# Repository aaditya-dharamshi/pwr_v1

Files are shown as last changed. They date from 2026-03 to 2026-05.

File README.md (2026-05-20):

# pwr_v1
Main powerboard (first version) PCB files.

This was the first major board designed for SeeGoals, a project under FIA Robotics at Linkoping University, Sweden. I designed the complete PCB (assisted by other teammates who have developed the foundation), and the design files are shared here with permission from LiU SeeGoals.

This was the prototype for the main power distribution and interface board for the robot, powered by a 23.8V LiPo battery. This board is designed with KiCAD 8, and this repository contains the KiCAD project files and related documents.

# Documentations
📄 [Schematic PDF](Docs%20and%20Images/pwr_v1_schematic.pdf)
📄 [Layout PDF ](Docs%20and%20Images/pwr_v1_CopperLayers.pdf)

# 3D renders
Top view
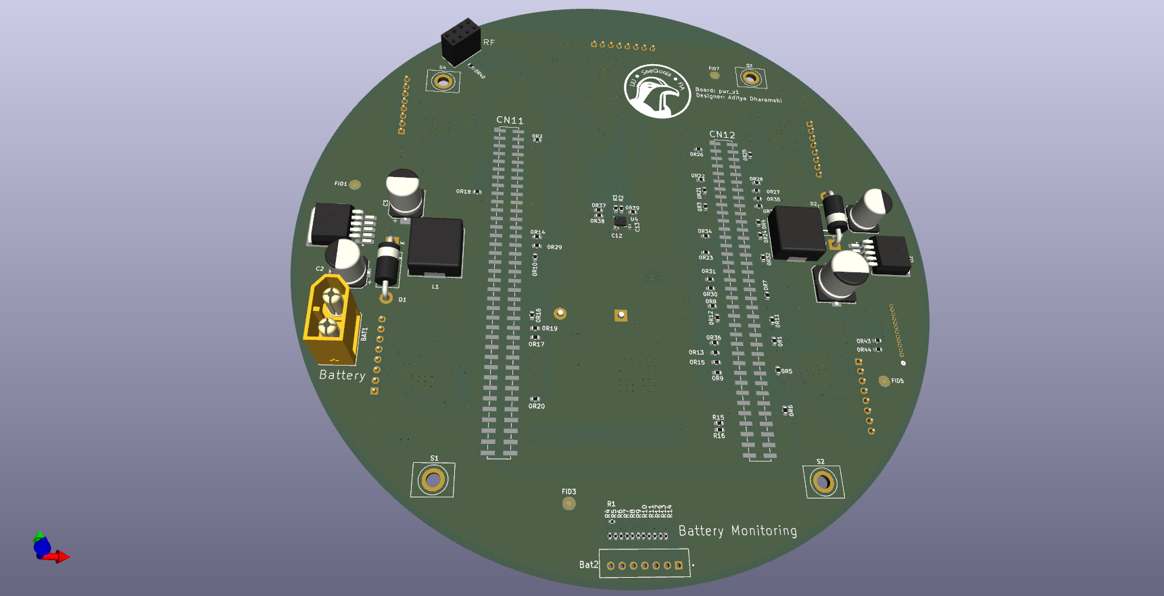
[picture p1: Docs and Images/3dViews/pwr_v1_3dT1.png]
Top Layer

Bottom view
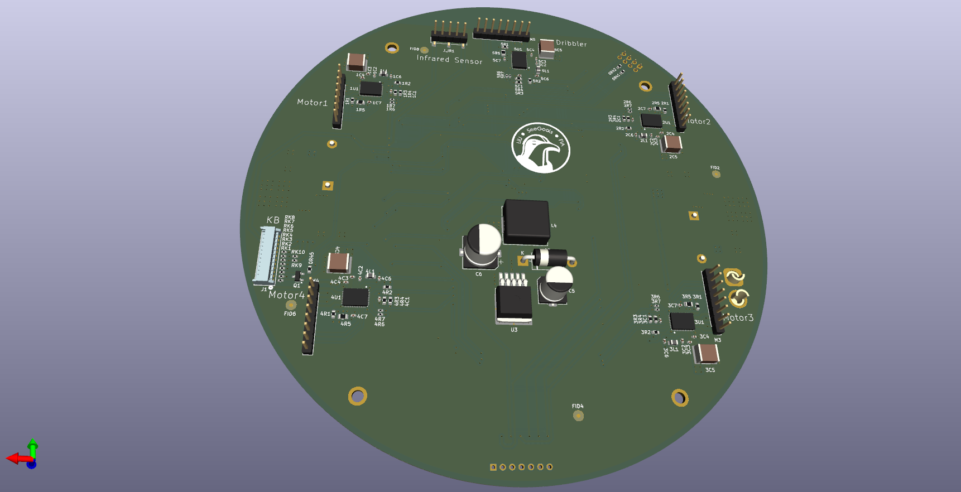
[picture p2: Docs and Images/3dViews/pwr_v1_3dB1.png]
Bottom Layer


Main features:
- 3.3V, 5V and 12V buck converters
- IMU on board
- Interfaces for STM32 Nucleo, nRF board and kicker board.

Stackup: 
- 4-layer FR4 PCB with 1.6mm thickness
- Copper thickness: 2 oz outer layer and 1 oz inner layers.

Design considerations:
- High-current power distribution from the LiPo battery.
- Dedicated power and signal layers.
- 4-layered stackup for improved grounding and power integrity.
- Decoupling capacitors placed carefully near the components.
- SMD-type connectors used for STM32 Nucleo interface, reducing thru hole pins and enabling better power and ground plane integrity.

Validation	
- This board was fabricated, assembled and integrated into the robot.
- During validation, issues related to nRF connector pin mapping, connector selection and mechanical design perspectivewere identified, which were addressed in the second revision.

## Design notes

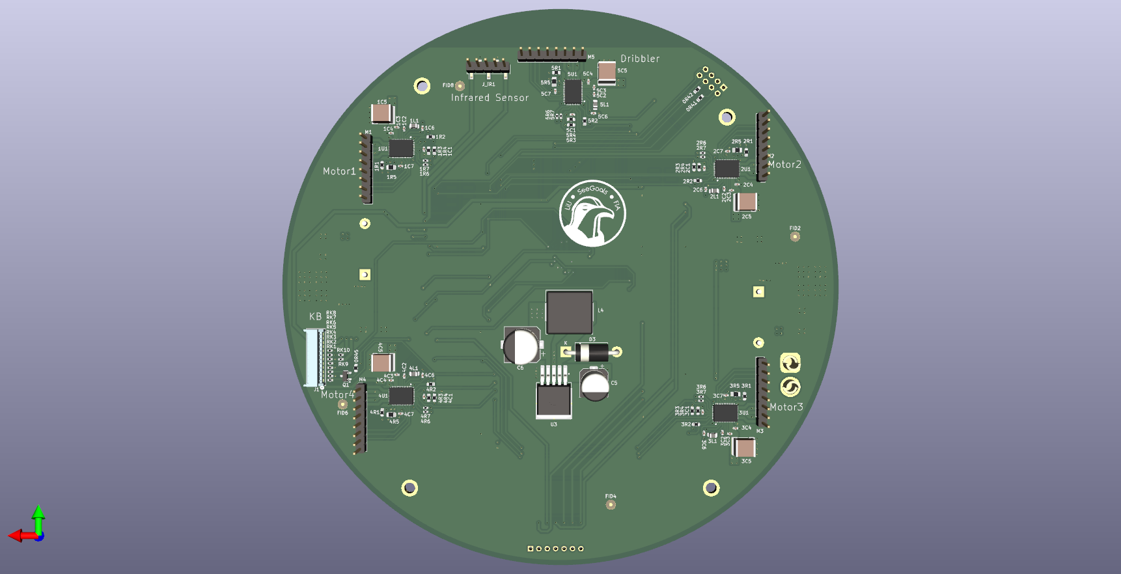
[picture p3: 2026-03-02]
Docs and Images/3dViews/pwr_v1_3dB.png

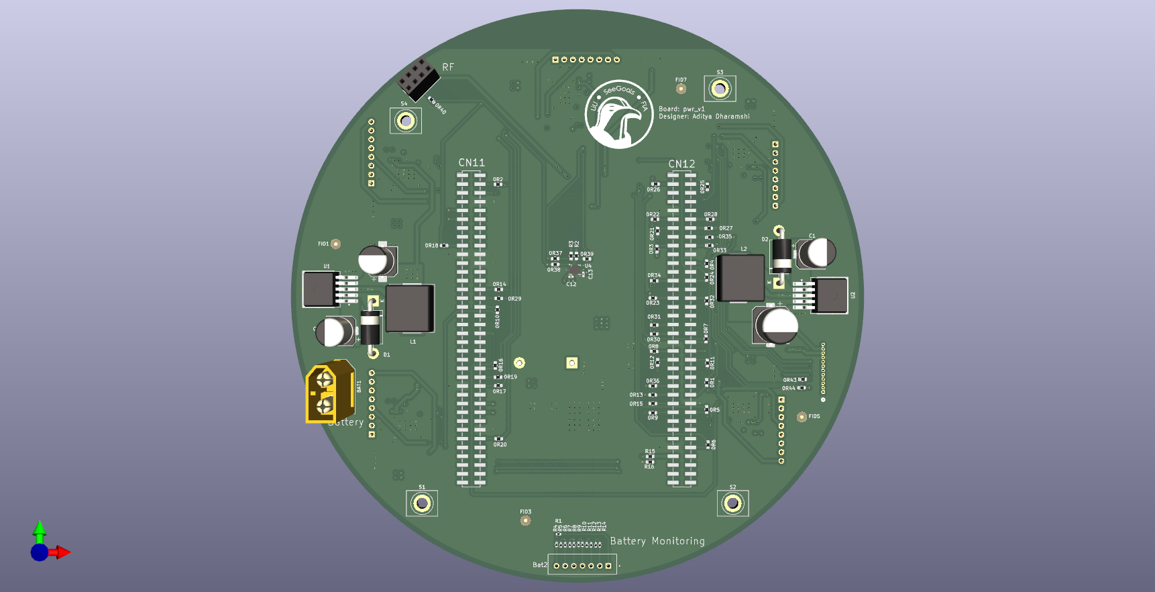
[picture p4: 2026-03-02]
Docs and Images/3dViews/pwr_v1_3dT.png

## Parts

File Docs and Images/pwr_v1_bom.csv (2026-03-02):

Value | Designator | Footprint | JLCPCB Part #?optional?
0 | 0R1,0R2,0R3,0R4,0R5,0R6,0R7,0R8,0R9,0R10,0R11,0R12,0R13,0R14,0R15,0R16,0R17,0R18,0R19,0R20,0R21,0R22,0R23,0R24,0R25,0R26,0R27,0R28,0R29,0R30,0R31,0R32,0R33,0R34,0R35,0R36,0R37,0R38,0R39,0R40,0R41,0R42,0R43,0R44,0R45 | Resistor_SMD:R_0603_1608Metric | C21189
100nF | 1C1 | Capacitor_SMD:C_0402_1005Metric | C1525
47nF | 1C2 | Capacitor_SMD:C_0402_1005Metric | C307339
1uF | 1C3 | Capacitor_SMD:C_0402_1005Metric | C14445
0.1uF | 1C4 | Capacitor_SMD:C_0402_1005Metric | C307331
22uF | 1C5 | Capacitor_SMD:C_2220_5750Metric | C784103
22uF | 1C6 | Capacitor_SMD:C_0402_1005Metric | C105226
1uF | 1C7 | Capacitor_SMD:C_0402_1005Metric | C76999
47uH | 1L1 | Inductor_SMD:L_0805_2012Metric | C105499
5k1 | 1R1,1R2 | Resistor_SMD:R_0603_1608Metric | C403509
27k | 1R3 | Resistor_SMD:R_0603_1608Metric | C22967
20k | 1R4 | Resistor_SMD:R_0603_1608Metric | C4184
1M | 1R5 | Resistor_SMD:R_0805_2012Metric | C107700
47k | 1R6 | Resistor_SMD:R_0402_1005Metric | C25792
22k | 1R7 | Resistor_SMD:R_0402_1005Metric | C25547
MCT8316Z0TRGFR | 1U1 | motorDriver:RGF0040E-IPC_B | C3681342
100nF | 2C1 | Capacitor_SMD:C_0402_1005Metric | C1525
47nF | 2C2 | Capacitor_SMD:C_0402_1005Metric | C307339
1uF | 2C3 | Capacitor_SMD:C_0402_1005Metric | C14445
0.1uF | 2C4 | Capacitor_SMD:C_0402_1005Metric | C307331
22uF | 2C5 | Capacitor_SMD:C_2220_5750Metric | C784103
22uF | 2C6 | Capacitor_SMD:C_0402_1005Metric | C105226
1uF | 2C7 | Capacitor_SMD:C_0402_1005Metric | C76999
47uH | 2L1 | Inductor_SMD:L_0805_2012Metric | C105499
5k1 | 2R1,2R2 | Resistor_SMD:R_0603_1608Metric | C403509
27k | 2R3 | Resistor_SMD:R_0603_1608Metric | C22967
20k | 2R4 | Resistor_SMD:R_0603_1608Metric | C4184
1M | 2R5 | Resistor_SMD:R_0805_2012Metric | C107700
47k | 2R6 | Resistor_SMD:R_0402_1005Metric | C25792
22k | 2R7 | Resistor_SMD:R_0402_1005Metric | C25547
MCT8316Z0TRGFR | 2U1 | motorDriver:RGF0040E-IPC_B | C3681342
100nF | 3C1 | Capacitor_SMD:C_0402_1005Metric | C1525
47nF | 3C2 | Capacitor_SMD:C_0402_1005Metric | C307339
1uF | 3C3 | Capacitor_SMD:C_0402_1005Metric | C14445
0.1uF | 3C4 | Capacitor_SMD:C_0402_1005Metric | C307331
22uF | 3C5 | Capacitor_SMD:C_2220_5750Metric | C784103
22uF | 3C6 | Capacitor_SMD:C_0402_1005Metric | C105226
1uF | 3C7 | Capacitor_SMD:C_0402_1005Metric | C76999
47uH | 3L1 | Inductor_SMD:L_0805_2012Metric | C105499
5k1 | 3R1,3R2 | Resistor_SMD:R_0603_1608Metric | C403509
27k | 3R3 | Resistor_SMD:R_0603_1608Metric | C22967
20k | 3R4 | Resistor_SMD:R_0603_1608Metric | C4184
1M | 3R5 | Resistor_SMD:R_0805_2012Metric | C107700
47k | 3R6 | Resistor_SMD:R_0402_1005Metric | C25792
22k | 3R7 | Resistor_SMD:R_0402_1005Metric | C25547
MCT8316Z0TRGFR | 3U1 | motorDriver:RGF0040E-IPC_B | C3681342
100nF | 4C1 | Capacitor_SMD:C_0402_1005Metric | C1525
47nF | 4C2 | Capacitor_SMD:C_0402_1005Metric | C307339
1uF | 4C3 | Capacitor_SMD:C_0402_1005Metric | C14445
0.1uF | 4C4 | Capacitor_SMD:C_0402_1005Metric | C307331
22uF | 4C5 | Capacitor_SMD:C_2220_5750Metric | C784103
22uF | 4C6 | Capacitor_SMD:C_0402_1005Metric | C105226
1uF | 4C7 | Capacitor_SMD:C_0402_1005Metric | C76999
47uH | 4L1 | Inductor_SMD:L_0805_2012Metric | C105499
5k1 | 4R1,4R2 | Resistor_SMD:R_0603_1608Metric | C403509
27k | 4R3 | Resistor_SMD:R_0603_1608Metric | C22967
20k | 4R4 | Resistor_SMD:R_0603_1608Metric | C4184
1M | 4R5 | Resistor_SMD:R_0805_2012Metric | C107700
47k | 4R6 | Resistor_SMD:R_0402_1005Metric | C25792
22k | 4R7 | Resistor_SMD:R_0402_1005Metric | C25547
MCT8316Z0TRGFR | 4U1 | motorDriver:RGF0040E-IPC_B | C3681342
100nF | 5C1 | Capacitor_SMD:C_0402_1005Metric | C1525
47nF | 5C2 | Capacitor_SMD:C_0402_1005Metric | C307339
1uF | 5C3 | Capacitor_SMD:C_0402_1005Metric | C14445
0.1uF | 5C4 | Capacitor_SMD:C_0402_1005Metric | C307331
22uF | 5C5 | Capacitor_SMD:C_2220_5750Metric | C784103
22uF | 5C6 | Capacitor_SMD:C_0402_1005Metric | C105226
1uF | 5C7 | Capacitor_SMD:C_0402_1005Metric | C76999
47uH | 5L1 | Inductor_SMD:L_0805_2012Metric | C105499
5k1 | 5R1,5R2 | Resistor_SMD:R_0603_1608Metric | C403509
27k | 5R3 | Resistor_SMD:R_0603_1608Metric | C22967
20k | 5R4 | Resistor_SMD:R_0603_1608Metric | C4184
1M | 5R5 | Resistor_SMD:R_0805_2012Metric | C107700
47k | 5R6 | Resistor_SMD:R_0402_1005Metric | C25792
22k | 5R7 | Resistor_SMD:R_0402_1005Metric | C25547
MCT8316Z0TRGFR | 5U1 | motorDriver:RGF0040E-IPC_B | C3681342
XT60 | BAT1 | Connector_AMASS:AMASS_XT60-M_1x02_P7.20mm_Vertical | C98733
Conn_01x07 | Bat2 | B7B_XH_A:JST_B7B-XH-A | C144398
100uF | C1,C2,C5 | Capacitor_SMD:CP_Elec_8x10 | C116241
1000uF | C3 | Capacitor_SMD:CP_Elec_8x10.5 | C280406
1000uF | C4,C6 | Capacitor_SMD:CP_Elec_10x10.5 | C401766
0.1uF | C12,C13 | Capacitor_SMD:C_0402_1005Metric | C307331
Conn_02x04_Counter_Clockwise | J_RF1 | Connector_PinSocket_2.54mm:PinSocket_2x04_P2.54mm_Vertical | C2977588
100uH | L1,L4 | Inductor_SMD:L_Sunlord_MWSA1206S-101 | C408533
150uH | L2 | Inductor_SMD:L_TaiTech_TMPC1265_13.5x12.5mm | C357258
Conn_01x08_Socket | M1,M2,M3,M4,M5 | Connector_PinHeader_2.54mm:PinHeader_1x08_P2.54mm_Vertical | C6332201
3k | R1,R5,R7,R9,R11,R13 | Resistor_SMD:R_0402_1005Metric | C278590
1k | R2,R3 | Resistor_SMD:R_0603_1608Metric | C21190
11k | R4,R6,R8,R10,R12,R14 | Resistor_SMD:R_0402_1005Metric | C413005
1M | R15 | Resistor_SMD:R_0603_1608Metric | C105578
100k | R16 | Resistor_SMD:R_0603_1608Metric | C25803
100 | RK1,RK2,RK3,RK4,RK5,RK6,RK7,RK8 | Resistor_SMD:R_0402_1005Metric | C412972
10k | RK9,RK10 | Resistor_SMD:R_0402_1005Metric | C25531
LM2576S-5 | U1 | Package_TO_SOT_SMD:TO-263-5_TabPin3 | C880552
LM2576S-12 | U2 | Package_TO_SOT_SMD:TO-263-5_TabPin3 | C16671
LM2576S-3.3 | U3 | Package_TO_SOT_SMD:TO-263-5_TabPin3 | C2863400
LSM6DSLTR | U4 | Package_LGA:LGA-14_3x2.5mm_P0.5mm_LayoutBorder3x4y | C126672

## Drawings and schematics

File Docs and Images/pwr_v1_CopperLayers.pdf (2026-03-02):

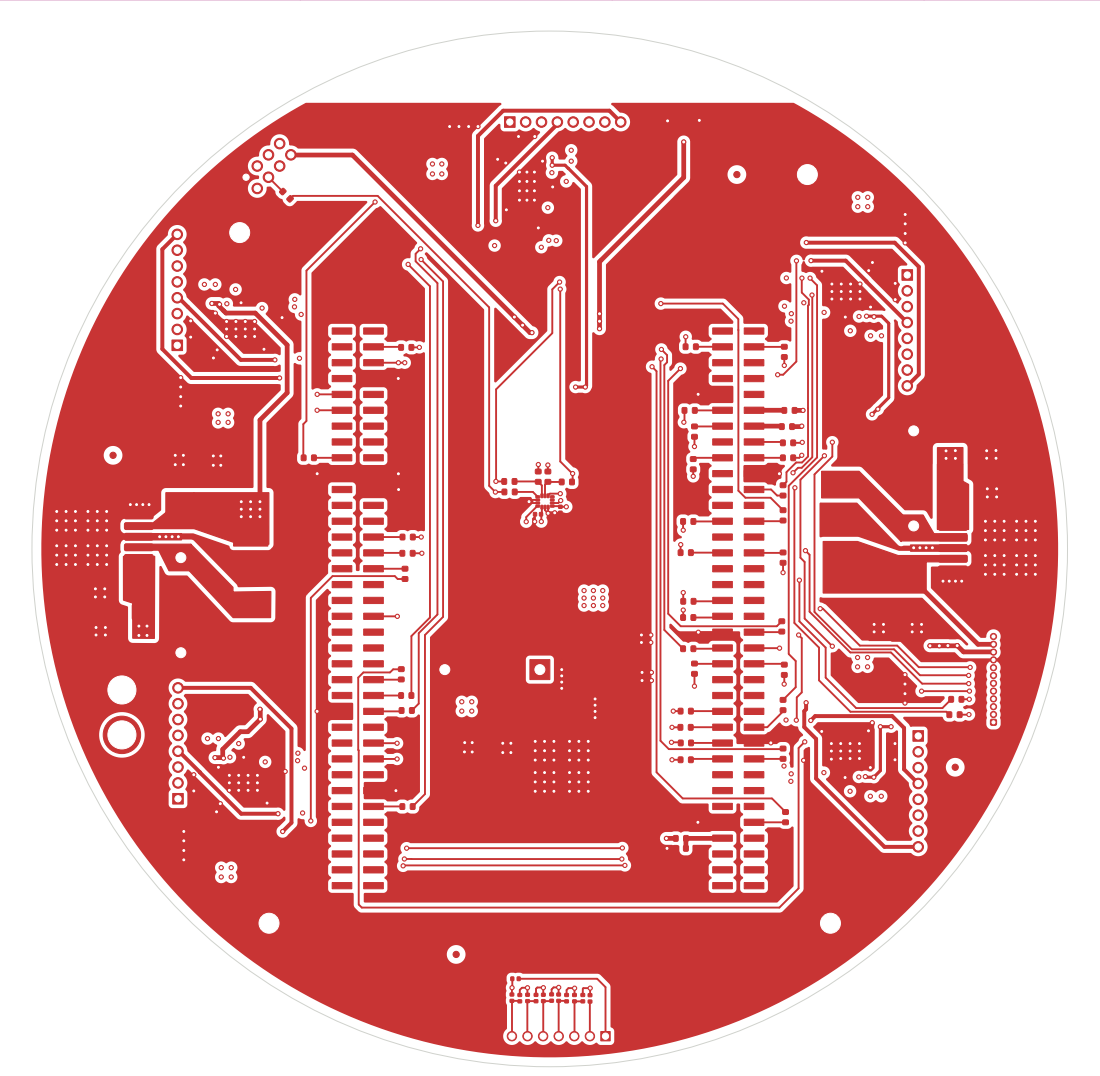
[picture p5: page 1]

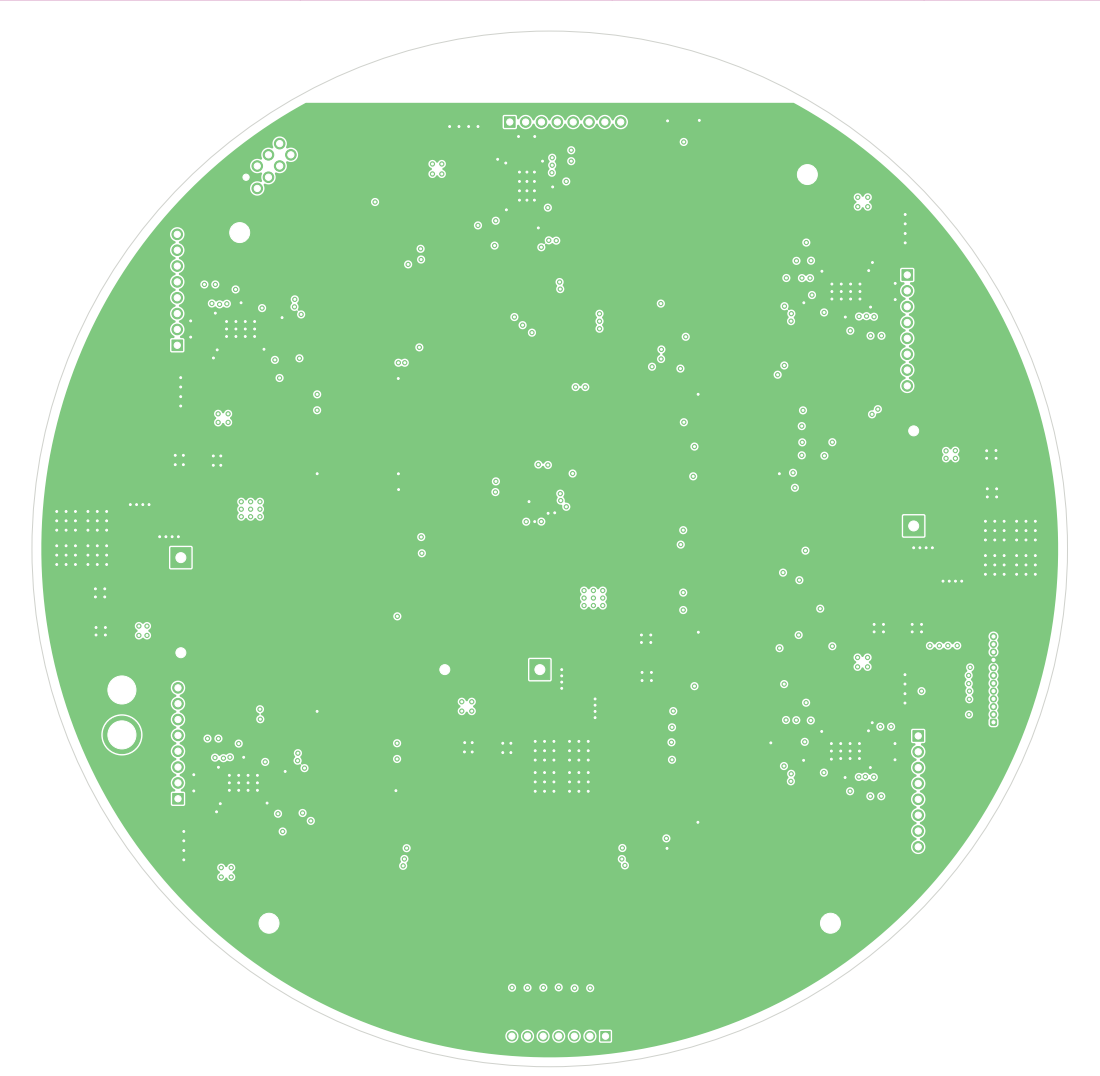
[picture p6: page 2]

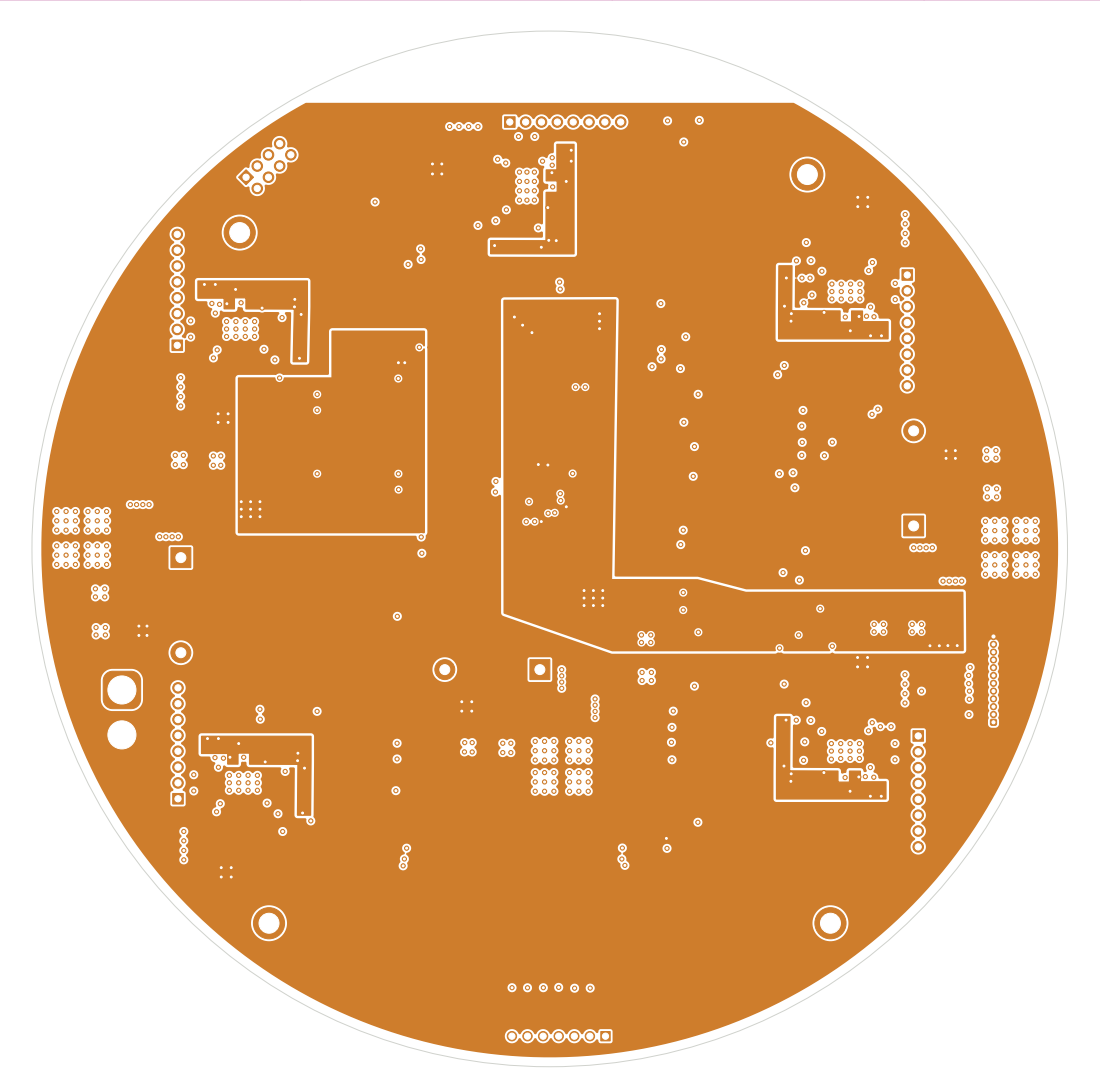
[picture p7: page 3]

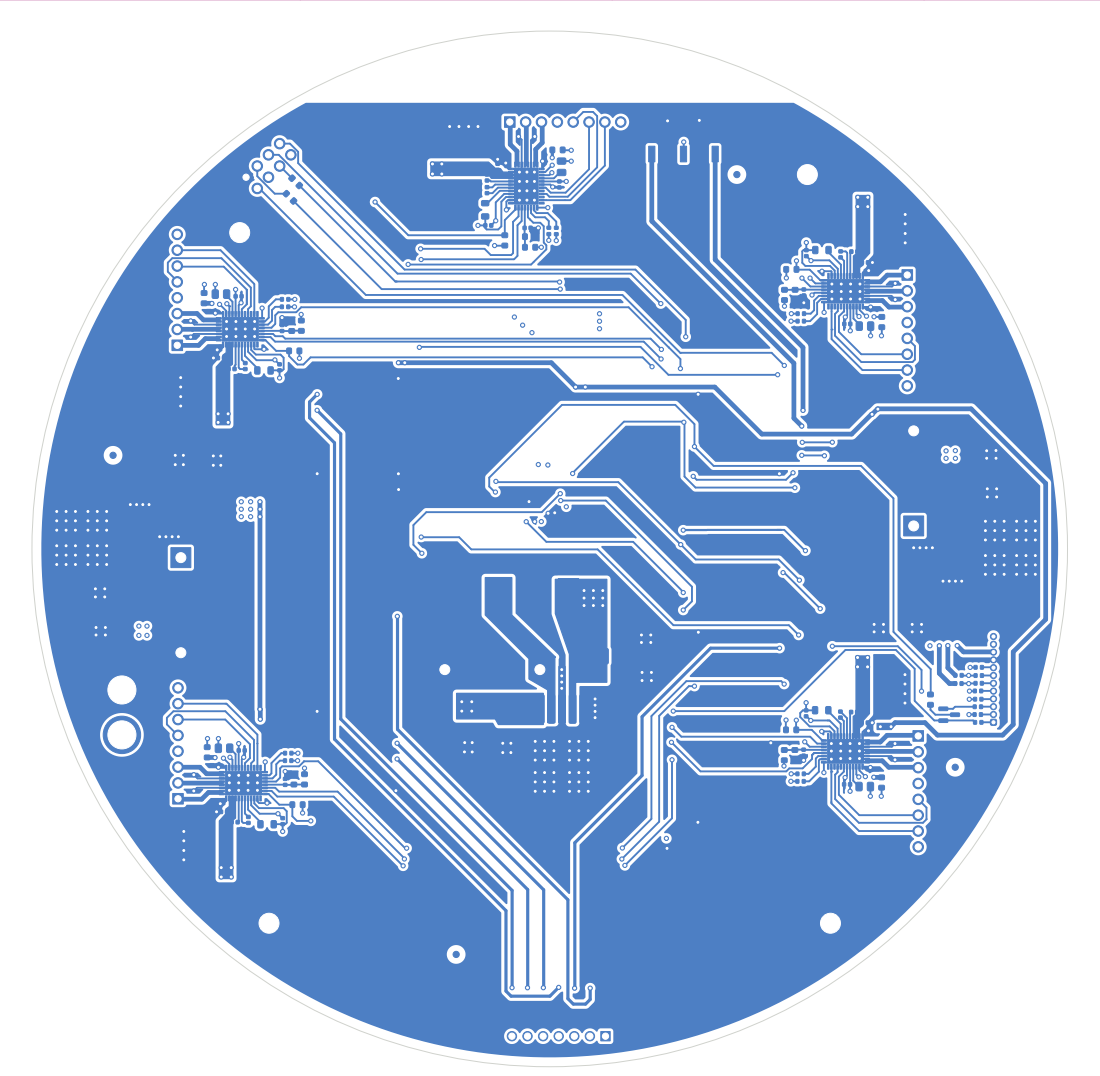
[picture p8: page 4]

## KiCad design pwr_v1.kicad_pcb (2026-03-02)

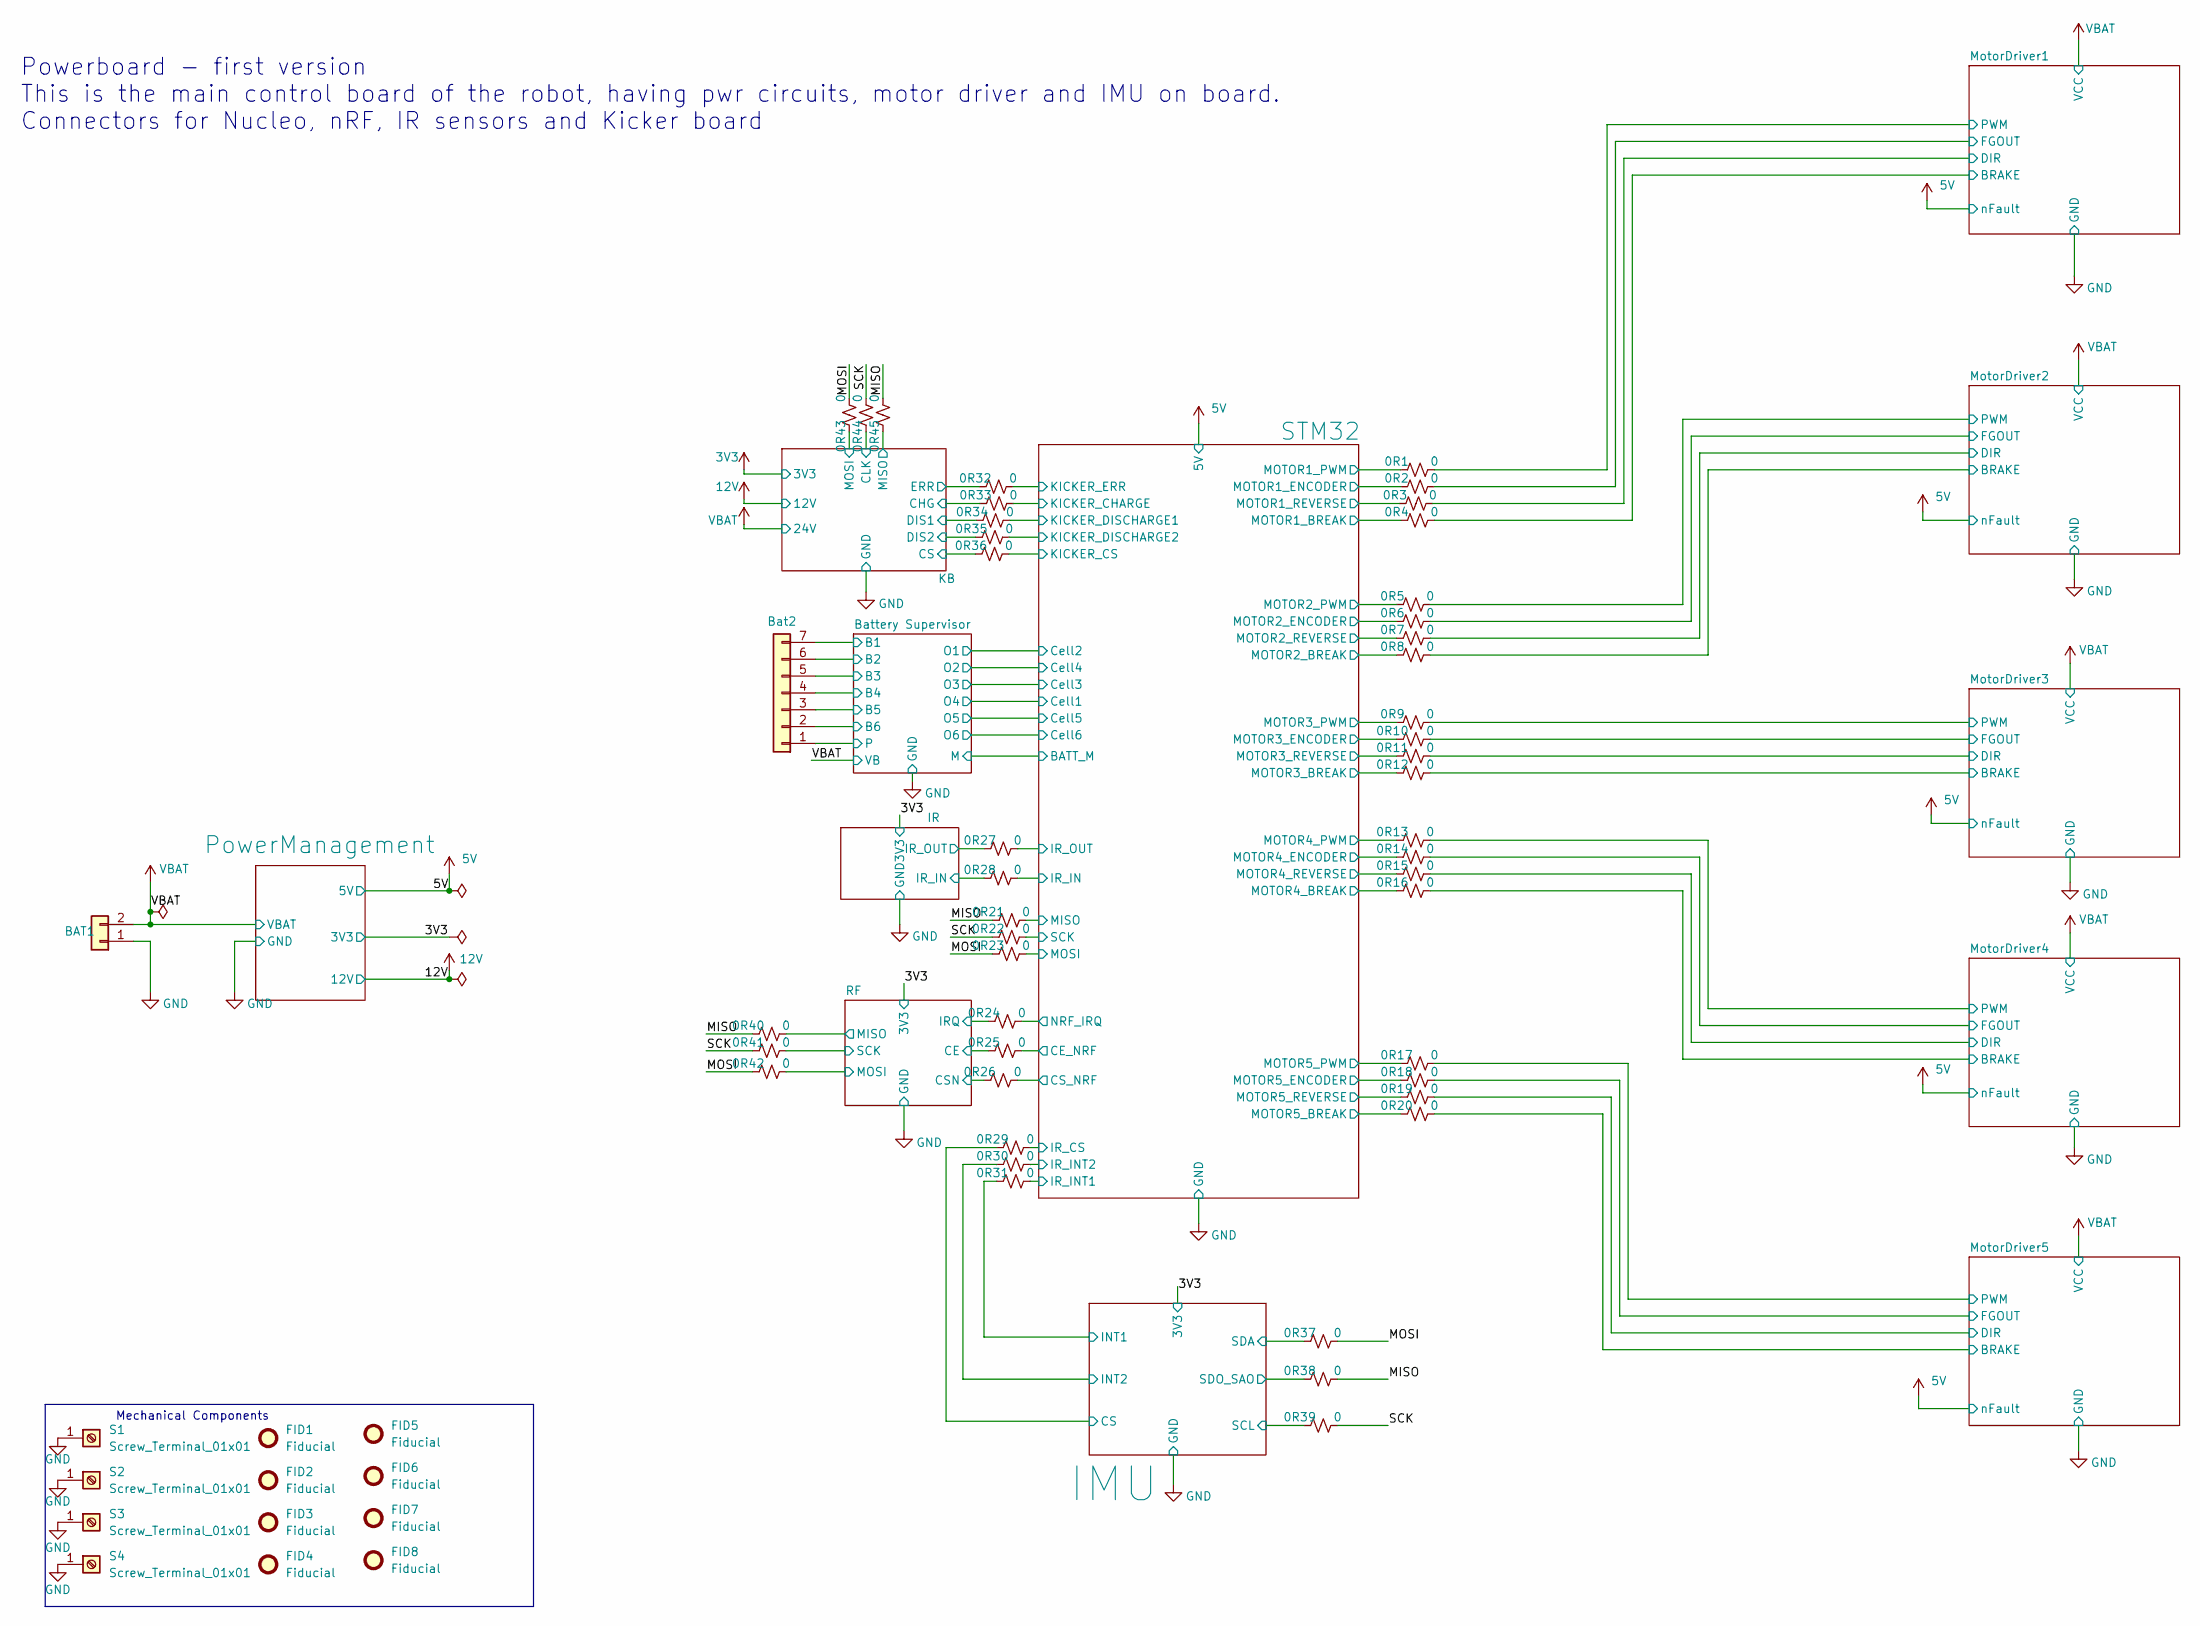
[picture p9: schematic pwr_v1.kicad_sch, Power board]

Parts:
0R1, 0R2, 0R3, 0R4, 0R5, 0R6, 0R7, 0R8, 0R9, 0R10, 0R11, 0R12, 0R13, 0R14, 0R15, 0R16, 0R17, 0R18, 0R19, 0R20, 0R21, 0R22, 0R23, 0R24, 0R25, 0R26, 0R27, 0R28, 0R29, 0R30, 0R31, 0R32, 0R33, 0R34, 0R35, 0R36, 0R37, 0R38, 0R39, 0R40, 0R41, 0R42, 0R43, 0R44, 0R45: 0; R_0603_1608Metric
BAT1: XT60; AMASS_XT60-M_1x02_P7.20mm_Vertical
Bat2: Conn_01x07; JST_B7B-XH-A
FID1, FID2, FID3, FID4, FID5, FID6, FID7, FID8: Fiducial; Fiducial_1mm_Mask3mm
S1, S2, S3, S4: Screw_Terminal_01x01; TerminalBlock_MetzConnect_360271_1x01_Horizontal_ScrewM3.0_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

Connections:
/Battery Supervisor/B1: Bat2.7; also elsewhere on the board
/Battery Supervisor/B2: Bat2.6; also elsewhere on the board
/Battery Supervisor/B3: Bat2.5; also elsewhere on the board
/Battery Supervisor/B4: Bat2.4; also elsewhere on the board
/Battery Supervisor/B5: Bat2.3; also elsewhere on the board
/Battery Supervisor/B6: Bat2.2; also elsewhere on the board
/Battery Supervisor/P: Bat2.1; also elsewhere on the board
/IMU/CS: 0R29.1; also elsewhere on the board
/IMU/INT1: 0R31.1; also elsewhere on the board
/IMU/INT2: 0R30.1; also elsewhere on the board
/IMU/SCL: 0R39.1; also elsewhere on the board
/IMU/SDA: 0R37.1; also elsewhere on the board
/IMU/SDO_SAO: 0R38.1; also elsewhere on the board
/IR/IR_IN: 0R28.1; also elsewhere on the board
/IR/IR_OUT: 0R27.1; also elsewhere on the board
/KB/CHG: 0R33.1; also elsewhere on the board
/KB/CLK: 0R44.1; also elsewhere on the board
/KB/CS: 0R36.1; also elsewhere on the board
/KB/DIS1: 0R34.1; also elsewhere on the board
/KB/DIS2: 0R35.1; also elsewhere on the board
/KB/ERR: 0R32.1; also elsewhere on the board
/KB/MISO: 0R45.1; also elsewhere on the board
/KB/MOSI: 0R43.1; also elsewhere on the board
/MISO: 0R21.1, 0R38.2, 0R40.1, 0R45.2
/MOSI: 0R23.1, 0R37.2, 0R42.1, 0R43.2
/MotorDriver1/BRAKE: 0R4.2; also elsewhere on the board
/MotorDriver1/DIR: 0R3.2; also elsewhere on the board
/MotorDriver1/FGOUT: 0R2.2; also elsewhere on the board
/MotorDriver1/PWM: 0R1.2; also elsewhere on the board
/MotorDriver2/BRAKE: 0R8.2; also elsewhere on the board
/MotorDriver2/DIR: 0R7.2; also elsewhere on the board
/MotorDriver2/FGOUT: 0R6.2; also elsewhere on the board
/MotorDriver2/PWM: 0R5.2; also elsewhere on the board
/MotorDriver3/BRAKE: 0R12.2; also elsewhere on the board
/MotorDriver3/DIR: 0R11.2; also elsewhere on the board
/MotorDriver3/FGOUT: 0R10.2; also elsewhere on the board
/MotorDriver3/PWM: 0R9.2; also elsewhere on the board
/MotorDriver4/BRAKE: 0R16.2; also elsewhere on the board
/MotorDriver4/DIR: 0R15.2; also elsewhere on the board
/MotorDriver4/FGOUT: 0R14.2; also elsewhere on the board
/MotorDriver4/PWM: 0R13.2; also elsewhere on the board
/MotorDriver5/BRAKE: 0R20.2; also elsewhere on the board
/MotorDriver5/DIR: 0R19.2; also elsewhere on the board
/MotorDriver5/FGOUT: 0R18.2; also elsewhere on the board
/MotorDriver5/PWM: 0R17.2; also elsewhere on the board
/RF/CE: 0R25.1; also elsewhere on the board
/RF/CSN: 0R26.1; also elsewhere on the board
/RF/IRQ: 0R24.1; also elsewhere on the board
/RF/MISO: 0R40.2; also elsewhere on the board
/RF/MOSI: 0R42.2; also elsewhere on the board
/RF/SCK: 0R41.2; also elsewhere on the board
/SCK: 0R22.1, 0R39.2, 0R41.1, 0R44.2
/STM32/CE_NRF: 0R25.2; also elsewhere on the board
/STM32/CS_NRF: 0R26.2; also elsewhere on the board
/STM32/IR_CS: 0R29.2; also elsewhere on the board
/STM32/IR_IN: 0R28.2; also elsewhere on the board
/STM32/IR_INT1: 0R31.2; also elsewhere on the board
/STM32/IR_INT2: 0R30.2; also elsewhere on the board
/STM32/IR_OUT: 0R27.2; also elsewhere on the board
/STM32/KICKER_CHARGE: 0R33.2; also elsewhere on the board
/STM32/KICKER_CS: 0R36.2; also elsewhere on the board
/STM32/KICKER_DISCHARGE1: 0R34.2; also elsewhere on the board
/STM32/KICKER_DISCHARGE2: 0R35.2; also elsewhere on the board
/STM32/KICKER_ERR: 0R32.2; also elsewhere on the board
/STM32/MISO: 0R21.2; also elsewhere on the board
/STM32/MOSI: 0R23.2; also elsewhere on the board
/STM32/MOTOR1_BREAK: 0R4.1; also elsewhere on the board
/STM32/MOTOR1_ENCODER: 0R2.1; also elsewhere on the board
/STM32/MOTOR1_PWM: 0R1.1; also elsewhere on the board
/STM32/MOTOR1_REVERSE: 0R3.1; also elsewhere on the board
/STM32/MOTOR2_BREAK: 0R8.1; also elsewhere on the board
/STM32/MOTOR2_ENCODER: 0R6.1; also elsewhere on the board
/STM32/MOTOR2_PWM: 0R5.1; also elsewhere on the board
/STM32/MOTOR2_REVERSE: 0R7.1; also elsewhere on the board
/STM32/MOTOR3_BREAK: 0R12.1; also elsewhere on the board
/STM32/MOTOR3_ENCODER: 0R10.1; also elsewhere on the board
/STM32/MOTOR3_PWM: 0R9.1; also elsewhere on the board
/STM32/MOTOR3_REVERSE: 0R11.1; also elsewhere on the board
/STM32/MOTOR4_BREAK: 0R16.1; also elsewhere on the board
/STM32/MOTOR4_ENCODER: 0R14.1; also elsewhere on the board
/STM32/MOTOR4_PWM: 0R13.1; also elsewhere on the board
/STM32/MOTOR4_REVERSE: 0R15.1; also elsewhere on the board
/STM32/MOTOR5_BREAK: 0R20.1; also elsewhere on the board
/STM32/MOTOR5_ENCODER: 0R18.1; also elsewhere on the board
/STM32/MOTOR5_PWM: 0R17.1; also elsewhere on the board
/STM32/MOTOR5_REVERSE: 0R19.1; also elsewhere on the board
/STM32/NRF_IRQ: 0R24.2; also elsewhere on the board
/STM32/SCK: 0R22.2; also elsewhere on the board
GND: BAT1.1, S1.1, S2.1, S3.1, S4.1; also elsewhere on the board
VBAT: BAT1.2; also elsewhere on the board

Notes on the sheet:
Mechanical Components
Powerboard - first version This is the main control board of the robot, having pwr circuits, motor driver and IMU on board. Connectors for Nucleo, nRF, IR sensors and Kicker board

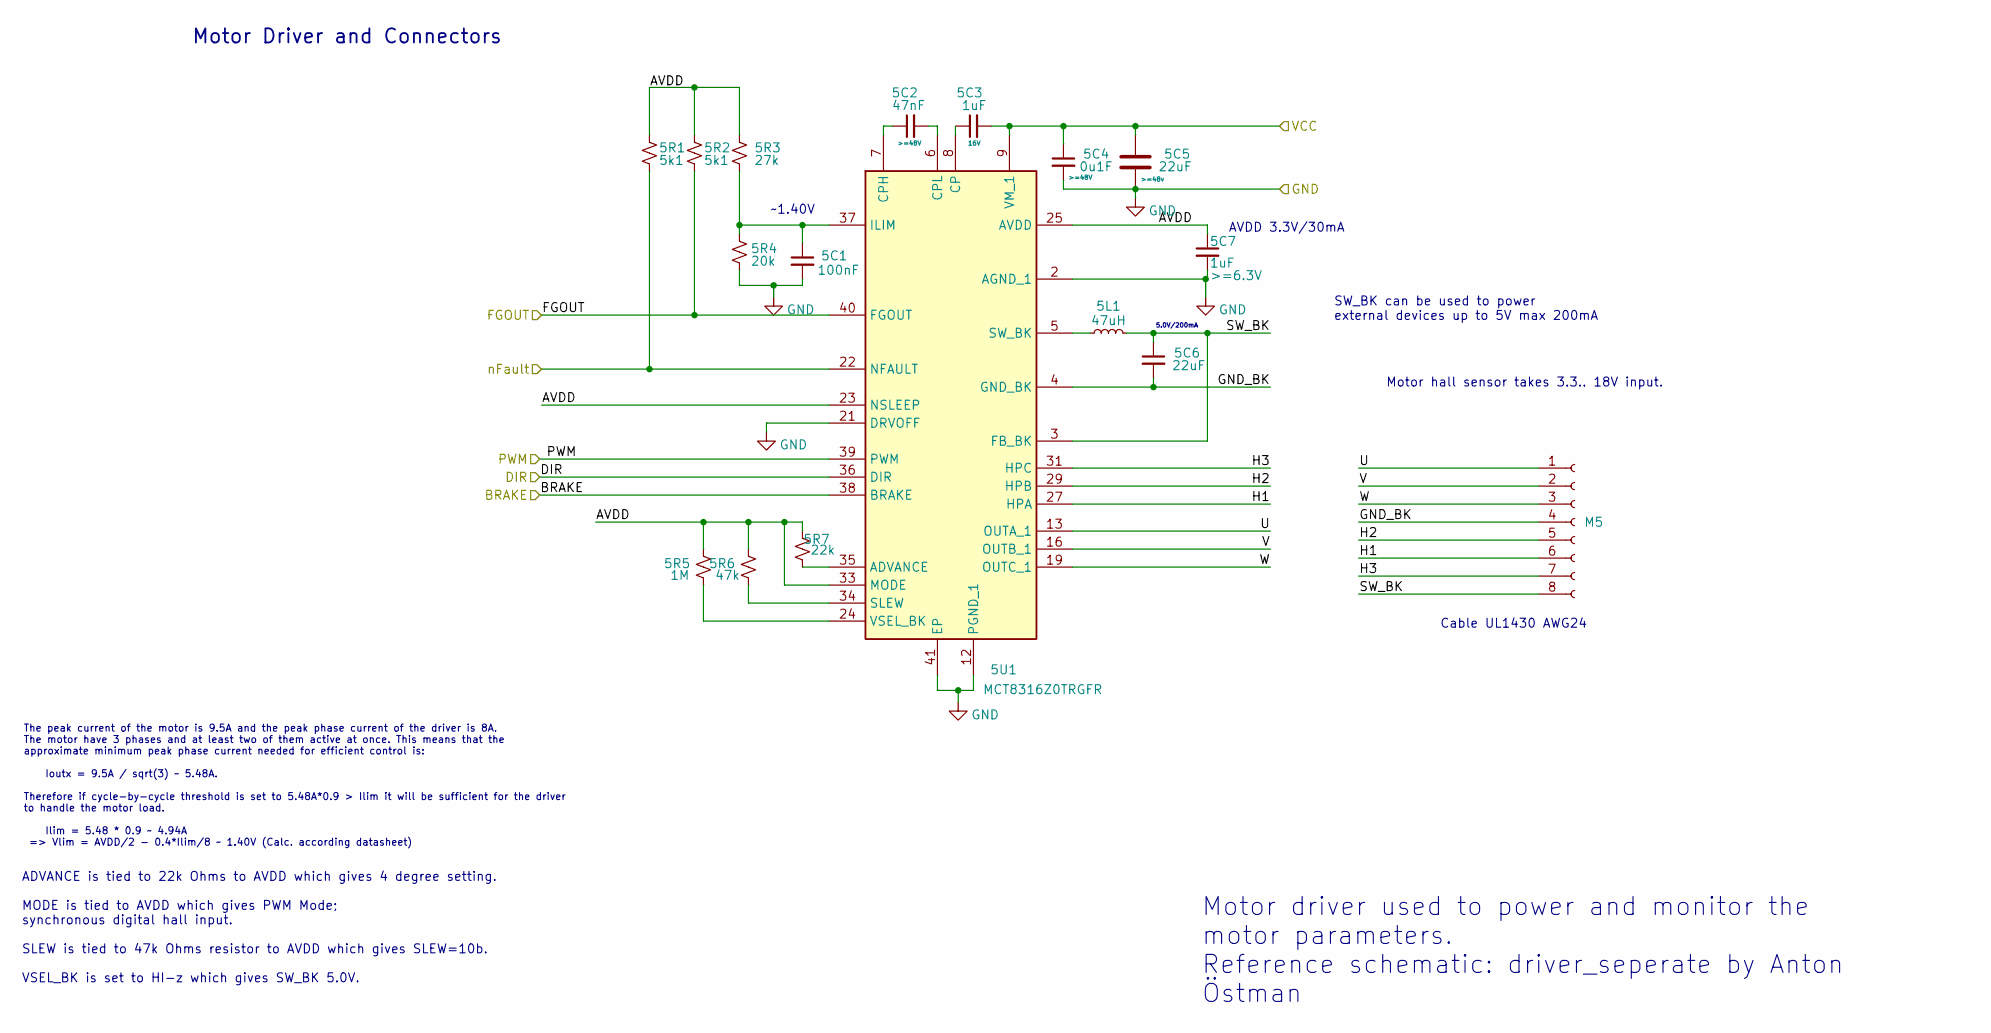
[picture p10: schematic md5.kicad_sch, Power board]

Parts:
5C1: 100nF; C_0402_1005Metric
5C2: 47nF; C_0402_1005Metric; Voltage >=48V
5C3: 1uF; C_0402_1005Metric; Voltage 16V
5C4: 0u1F; C_0402_1005Metric; Voltage >=48V
5C5: 22uF; C_2220_5750Metric; Voltage >=48v
5C6: 22uF; C_0402_1005Metric
5C7: 1uF; C_0402_1005Metric; Voltage >=6.3V
5L1: 47uH; L_0805_2012Metric
5R1, 5R2: 5k1; R_0603_1608Metric
5R3: 27k; R_0603_1608Metric
5R4: 20k; R_0603_1608Metric
5R5: 1M; R_0805_2012Metric
5R6: 47k; R_0402_1005Metric
5R7: 22k; R_0402_1005Metric
5U1: MCT8316Z0TRGFR; RGF0040E-IPC_B; Mouser Part Number 595-CT8316Z0TQRGFRQ1
M5: Conn_01x08_Socket; PinHeader_1x08_P2.54mm_Vertical

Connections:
5V: 5R1.2, 5U1.22 (NFAULT); also elsewhere on the board
/MotorDriver5/AVDD: 5C7.1, 5R1.1, 5R2.1, 5R3.1, 5R5.2, 5R6.2, 5R7.2, 5U1.23 (NSLEEP), 5U1.25 (AVDD), 5U1.33 (MODE)
/MotorDriver5/BRAKE: 5U1.38 (BRAKE); also elsewhere on the board
/MotorDriver5/DIR: 5U1.36 (DIR); also elsewhere on the board
/MotorDriver5/FGOUT: 5R2.2, 5U1.40 (FGOUT); also elsewhere on the board
/MotorDriver5/GND_BK: 5C6.2, 5U1.4 (GND_BK), M5.4
/MotorDriver5/H1: 5U1.27 (HPA), M5.6
/MotorDriver5/H2: 5U1.29 (HPB), M5.5
/MotorDriver5/H3: 5U1.31 (HPC), M5.7
/MotorDriver5/PWM: 5U1.39 (PWM); also elsewhere on the board
/MotorDriver5/SW_BK: 5C6.1, 5L1.2, 5U1.3 (FB_BK), M5.8
/MotorDriver5/U: 5U1.13 (OUTA_1), 5U1.14 (OUTA_2), M5.1
/MotorDriver5/V: 5U1.16 (OUTB_1), 5U1.17 (OUTB_2), M5.2
/MotorDriver5/W: 5U1.19 (OUTC_1), 5U1.20 (OUTC_2), M5.3
GND: 5C1.2, 5C4.2, 5C5.2, 5C7.2, 5R4.2, 5U1.2 (AGND_1), 5U1.12 (PGND_1), 5U1.15 (PGND_2), 5U1.18 (PGND_3), 5U1.21 (DRVOFF), 5U1.26 (AGND_2), 5U1.41 (EP); also elsewhere on the board
unnamed: 5R7.1, 5U1.35 (ADVANCE)
unnamed: 5C3.1, 5U1.8 (CP)
unnamed: 5C2.1, 5U1.7 (CPH)
unnamed: 5C2.2, 5U1.6 (CPL)
unnamed: 5C1.1, 5R3.2, 5R4.1, 5U1.37 (ILIM)
unnamed: 5R6.1, 5U1.34 (SLEW)
unnamed: 5L1.1, 5U1.5 (SW_BK)
unnamed: 5R5.1, 5U1.24 (VSEL_BK)
VBAT: 5C3.2, 5C4.1, 5C5.1, 5U1.9 (VM_1), 5U1.10 (VM_2), 5U1.11 (VM_3); also elsewhere on the board

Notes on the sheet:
SW_BK can be used to power external devices up to 5V max 200mA
5.0V/200mA
Cable UL1430 AWG24
ADVANCE is tied to 22k Ohms to AVDD which gives 4 degree setting. MODE is tied to AVDD which gives PWM Mode; synchronous digital hall input. SLEW is tied to 47k Ohms resistor to AVDD which gives SLEW=10b. VSEL_BK is set to HI-z which gives SW_BK 5.0V.
~1.40V
AVDD 3.3V/30mA
Motor Driver and Connectors
Motor hall sensor takes 3.3.. 18V input.
The peak current of the motor is 9.5A and the peak phase current of the driver is 8A. The motor have 3 phases and at least two of them active at once. This means that the approximate minimum peak phase current needed for efficient control is: Ioutx = 9.5A / sqrt(3) ~ 5.48A. Therefore if cycle-by-cy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
Motor driver used to power and monitor the motor parameters. Reference schematic: driver_seperate by Anton Östman

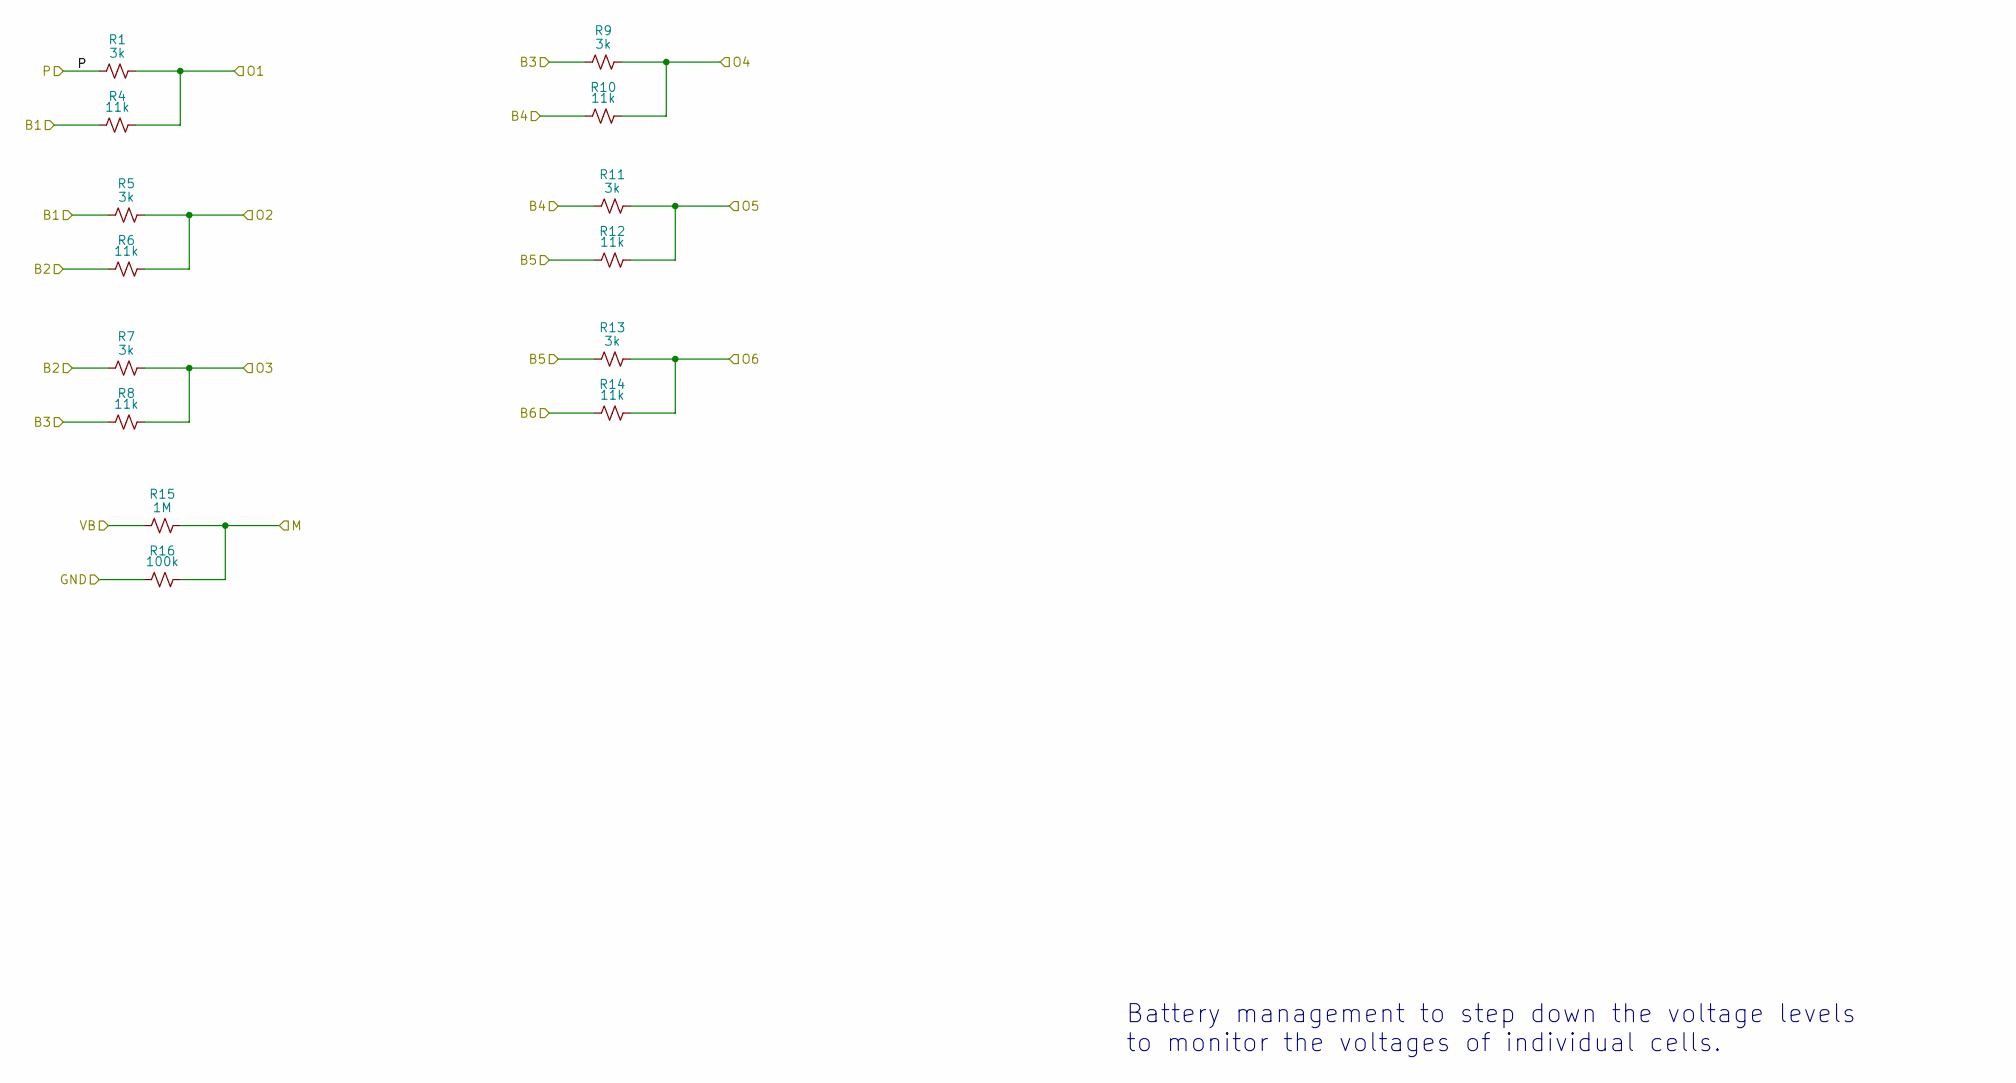
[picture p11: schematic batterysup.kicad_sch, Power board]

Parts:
R1, R5, R7, R9, R11, R13: 3k; R_0402_1005Metric
R4, R6, R8, R10, R12, R14: 11k; R_0402_1005Metric
R15: 1M; R_0603_1608Metric
R16: 100k; R_0603_1608Metric

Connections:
/Battery Supervisor/B1: R4.1, R5.1; also elsewhere on the board
/Battery Supervisor/B2: R6.1, R7.1; also elsewhere on the board
/Battery Supervisor/B3: R8.1, R9.1; also elsewhere on the board
/Battery Supervisor/B4: R10.1, R11.1; also elsewhere on the board
/Battery Supervisor/B5: R12.1, R13.1; also elsewhere on the board
/Battery Supervisor/B6: R14.1; also elsewhere on the board
/Battery Supervisor/M: R15.2, R16.2; also elsewhere on the board
/Battery Supervisor/O1: R1.2, R4.2; also elsewhere on the board
/Battery Supervisor/O2: R5.2, R6.2; also elsewhere on the board
/Battery Supervisor/O3: R7.2, R8.2; also elsewhere on the board
/Battery Supervisor/O4: R9.2, R10.2; also elsewhere on the board
/Battery Supervisor/O5: R11.2, R12.2; also elsewhere on the board
/Battery Supervisor/O6: R13.2, R14.2; also elsewhere on the board
/Battery Supervisor/P: R1.1; also elsewhere on the board
GND: R16.1; also elsewhere on the board
VBAT: R15.1; also elsewhere on the board

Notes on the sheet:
Battery management to step down the voltage levels to monitor the voltages of individual cells.

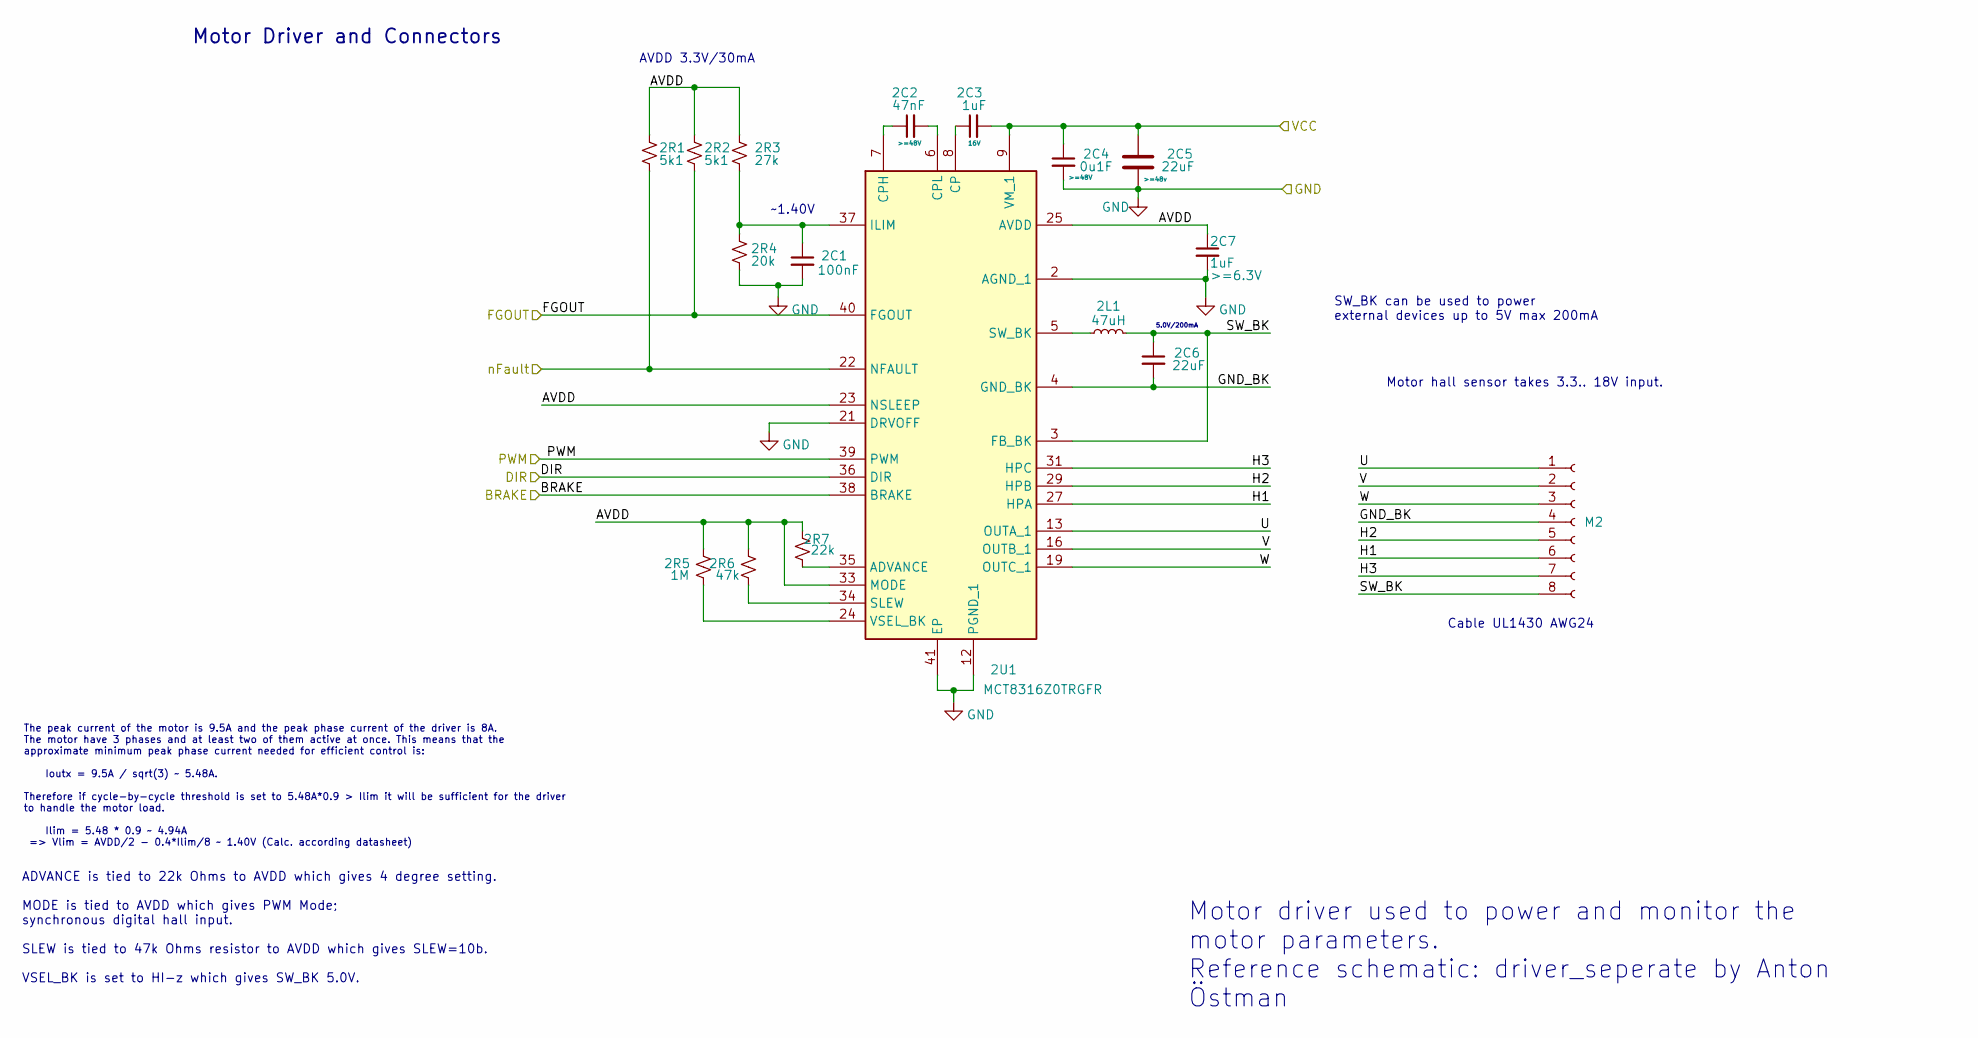
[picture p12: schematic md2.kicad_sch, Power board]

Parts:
2C1: 100nF; C_0402_1005Metric
2C2: 47nF; C_0402_1005Metric; Voltage >=48V
2C3: 1uF; C_0402_1005Metric; Voltage 16V
2C4: 0u1F; C_0402_1005Metric; Voltage >=48V
2C5: 22uF; C_2220_5750Metric; Voltage >=48v
2C6: 22uF; C_0402_1005Metric
2C7: 1uF; C_0402_1005Metric; Voltage >=6.3V
2L1: 47uH; L_0805_2012Metric
2R1, 2R2: 5k1; R_0603_1608Metric
2R3: 27k; R_0603_1608Metric
2R4: 20k; R_0603_1608Metric
2R5: 1M; R_0805_2012Metric
2R6: 47k; R_0402_1005Metric
2R7: 22k; R_0402_1005Metric
2U1: MCT8316Z0TRGFR; RGF0040E-IPC_B; Mouser Part Number 595-CT8316Z0TQRGFRQ1
M2: Conn_01x08_Socket; PinHeader_1x08_P2.54mm_Vertical

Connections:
5V: 2R1.2, 2U1.22 (NFAULT); also elsewhere on the board
/MotorDriver2/AVDD: 2C7.1, 2R1.1, 2R2.1, 2R3.1, 2R5.2, 2R6.2, 2R7.2, 2U1.23 (NSLEEP), 2U1.25 (AVDD), 2U1.33 (MODE)
/MotorDriver2/BRAKE: 2U1.38 (BRAKE); also elsewhere on the board
/MotorDriver2/DIR: 2U1.36 (DIR); also elsewhere on the board
/MotorDriver2/FGOUT: 2R2.2, 2U1.40 (FGOUT); also elsewhere on the board
/MotorDriver2/GND_BK: 2C6.2, 2U1.4 (GND_BK), M2.4
/MotorDriver2/H1: 2U1.27 (HPA), M2.6
/MotorDriver2/H2: 2U1.29 (HPB), M2.5
/MotorDriver2/H3: 2U1.31 (HPC), M2.7
/MotorDriver2/PWM: 2U1.39 (PWM); also elsewhere on the board
/MotorDriver2/SW_BK: 2C6.1, 2L1.2, 2U1.3 (FB_BK), M2.8
/MotorDriver2/U: 2U1.13 (OUTA_1), 2U1.14 (OUTA_2), M2.1
/MotorDriver2/V: 2U1.16 (OUTB_1), 2U1.17 (OUTB_2), M2.2
/MotorDriver2/W: 2U1.19 (OUTC_1), 2U1.20 (OUTC_2), M2.3
GND: 2C1.2, 2C4.2, 2C5.2, 2C7.2, 2R4.2, 2U1.2 (AGND_1), 2U1.12 (PGND_1), 2U1.15 (PGND_2), 2U1.18 (PGND_3), 2U1.21 (DRVOFF), 2U1.26 (AGND_2), 2U1.41 (EP); also elsewhere on the board
unnamed: 2R7.1, 2U1.35 (ADVANCE)
unnamed: 2C3.1, 2U1.8 (CP)
unnamed: 2C2.1, 2U1.7 (CPH)
unnamed: 2C2.2, 2U1.6 (CPL)
unnamed: 2C1.1, 2R3.2, 2R4.1, 2U1.37 (ILIM)
unnamed: 2R6.1, 2U1.34 (SLEW)
unnamed: 2L1.1, 2U1.5 (SW_BK)
unnamed: 2R5.1, 2U1.24 (VSEL_BK)
VBAT: 2C3.2, 2C4.1, 2C5.1, 2U1.9 (VM_1), 2U1.10 (VM_2), 2U1.11 (VM_3); also elsewhere on the board

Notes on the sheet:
SW_BK can be used to power external devices up to 5V max 200mA
ADVANCE is tied to 22k Ohms to AVDD which gives 4 degree setting. MODE is tied to AVDD which gives PWM Mode; synchronous digital hall input. SLEW is tied to 47k Ohms resistor to AVDD which gives SLEW=10b. VSEL_BK is set to HI-z which gives SW_BK 5.0V.
~1.40V
Motor Driver and Connectors
Cable UL1430 AWG24
AVDD 3.3V/30mA
The peak current of the motor is 9.5A and the peak phase current of the driver is 8A. The motor have 3 phases and at least two of them active at once. This means that the approximate minimum peak phase current needed for efficient control is: Ioutx = 9.5A / sqrt(3) ~ 5.48A. Therefore if cycle-by-cy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
Motor hall sensor takes 3.3.. 18V input.
5.0V/200mA
Motor driver used to power and monitor the motor parameters. Reference schematic: driver_seperate by Anton Östman

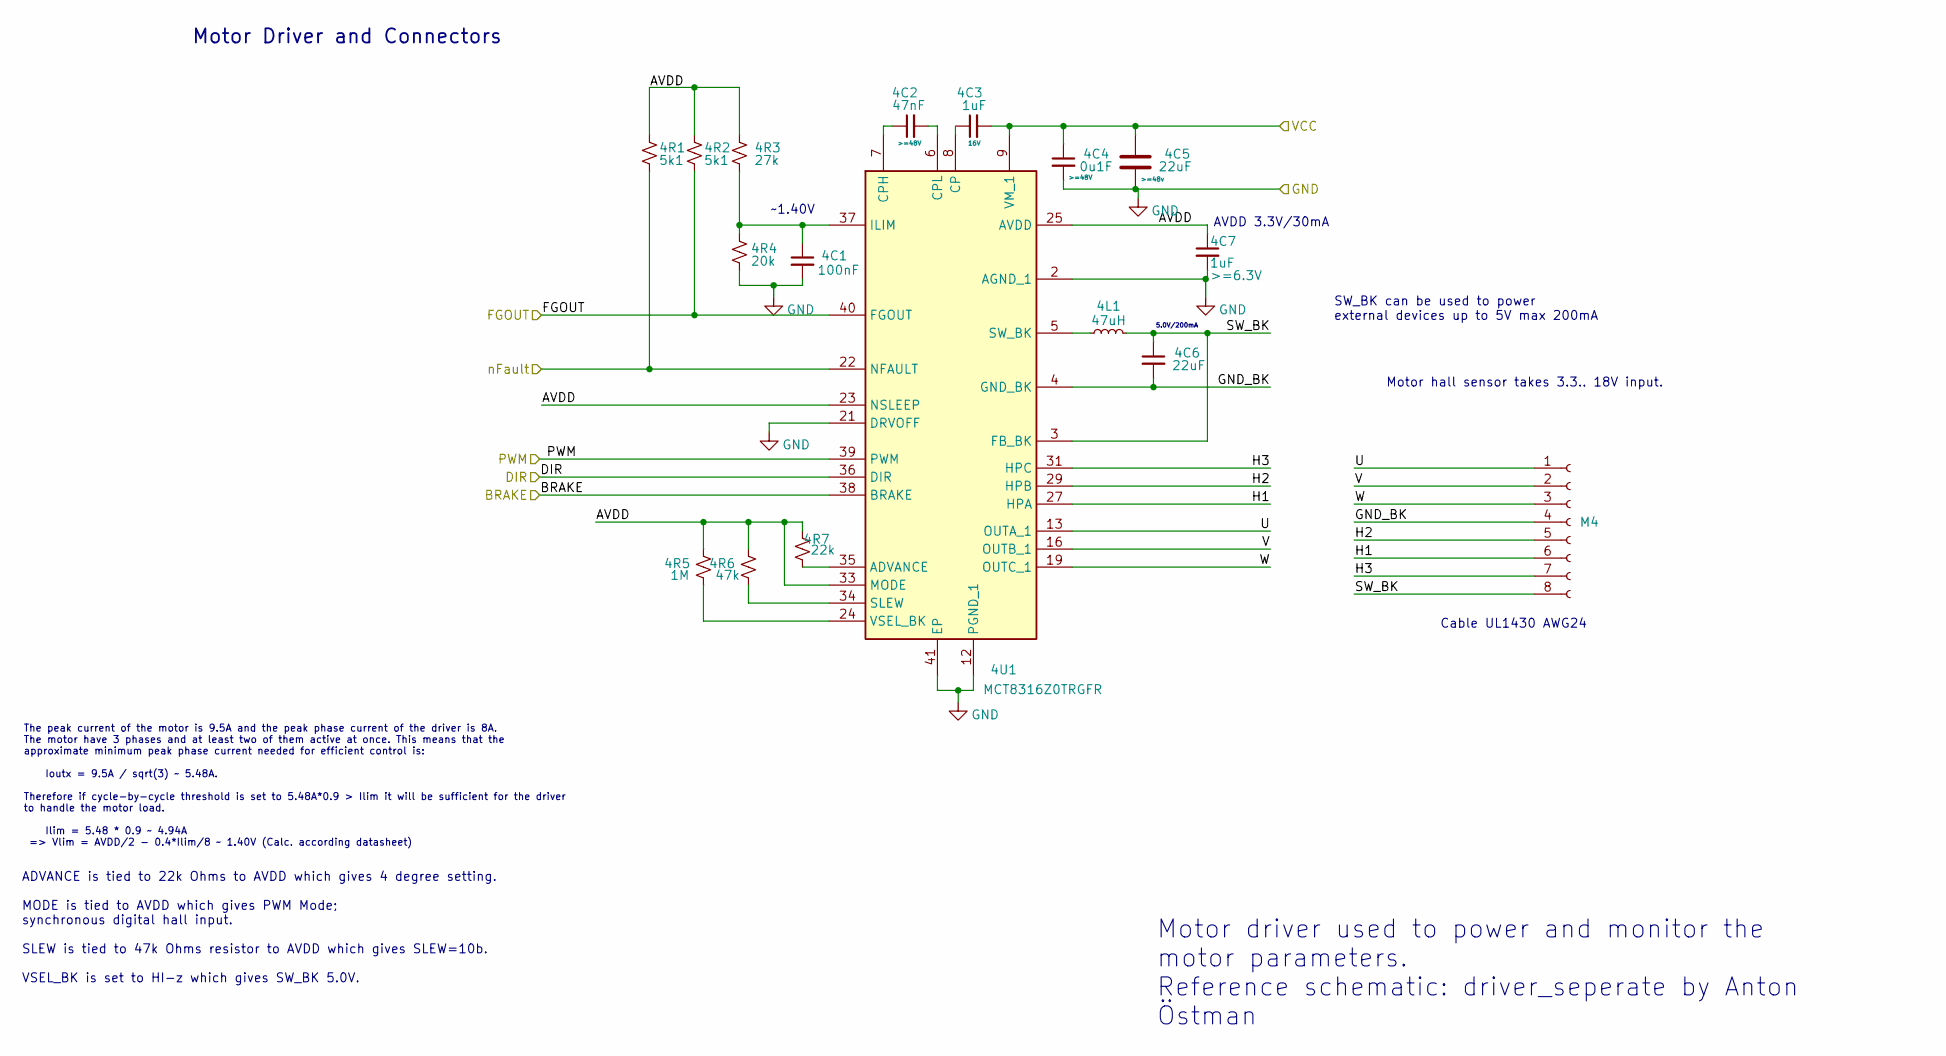
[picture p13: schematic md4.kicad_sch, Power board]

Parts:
4C1: 100nF; C_0402_1005Metric
4C2: 47nF; C_0402_1005Metric; Voltage >=48V
4C3: 1uF; C_0402_1005Metric; Voltage 16V
4C4: 0u1F; C_0402_1005Metric; Voltage >=48V
4C5: 22uF; C_2220_5750Metric; Voltage >=48v
4C6: 22uF; C_0402_1005Metric
4C7: 1uF; C_0402_1005Metric; Voltage >=6.3V
4L1: 47uH; L_0805_2012Metric
4R1, 4R2: 5k1; R_0603_1608Metric
4R3: 27k; R_0603_1608Metric
4R4: 20k; R_0603_1608Metric
4R5: 1M; R_0805_2012Metric
4R6: 47k; R_0402_1005Metric
4R7: 22k; R_0402_1005Metric
4U1: MCT8316Z0TRGFR; RGF0040E-IPC_B; Mouser Part Number 595-CT8316Z0TQRGFRQ1
M4: Conn_01x08_Socket; PinHeader_1x08_P2.54mm_Vertical

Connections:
5V: 4R1.2, 4U1.22 (NFAULT); also elsewhere on the board
/MotorDriver4/AVDD: 4C7.1, 4R1.1, 4R2.1, 4R3.1, 4R5.2, 4R6.2, 4R7.2, 4U1.23 (NSLEEP), 4U1.25 (AVDD), 4U1.33 (MODE)
/MotorDriver4/BRAKE: 4U1.38 (BRAKE); also elsewhere on the board
/MotorDriver4/DIR: 4U1.36 (DIR); also elsewhere on the board
/MotorDriver4/FGOUT: 4R2.2, 4U1.40 (FGOUT); also elsewhere on the board
/MotorDriver4/GND_BK: 4C6.2, 4U1.4 (GND_BK), M4.4
/MotorDriver4/H1: 4U1.27 (HPA), M4.6
/MotorDriver4/H2: 4U1.29 (HPB), M4.5
/MotorDriver4/H3: 4U1.31 (HPC), M4.7
/MotorDriver4/PWM: 4U1.39 (PWM); also elsewhere on the board
/MotorDriver4/SW_BK: 4C6.1, 4L1.2, 4U1.3 (FB_BK), M4.8
/MotorDriver4/U: 4U1.13 (OUTA_1), 4U1.14 (OUTA_2), M4.1
/MotorDriver4/V: 4U1.16 (OUTB_1), 4U1.17 (OUTB_2), M4.2
/MotorDriver4/W: 4U1.19 (OUTC_1), 4U1.20 (OUTC_2), M4.3
GND: 4C1.2, 4C4.2, 4C5.2, 4C7.2, 4R4.2, 4U1.2 (AGND_1), 4U1.12 (PGND_1), 4U1.15 (PGND_2), 4U1.18 (PGND_3), 4U1.21 (DRVOFF), 4U1.26 (AGND_2), 4U1.41 (EP); also elsewhere on the board
unnamed: 4R7.1, 4U1.35 (ADVANCE)
unnamed: 4C3.1, 4U1.8 (CP)
unnamed: 4C2.1, 4U1.7 (CPH)
unnamed: 4C2.2, 4U1.6 (CPL)
unnamed: 4C1.1, 4R3.2, 4R4.1, 4U1.37 (ILIM)
unnamed: 4R6.1, 4U1.34 (SLEW)
unnamed: 4L1.1, 4U1.5 (SW_BK)
unnamed: 4R5.1, 4U1.24 (VSEL_BK)
VBAT: 4C3.2, 4C4.1, 4C5.1, 4U1.9 (VM_1), 4U1.10 (VM_2), 4U1.11 (VM_3); also elsewhere on the board

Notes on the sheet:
Cable UL1430 AWG24
ADVANCE is tied to 22k Ohms to AVDD which gives 4 degree setting. MODE is tied to AVDD which gives PWM Mode; synchronous digital hall input. SLEW is tied to 47k Ohms resistor to AVDD which gives SLEW=10b. VSEL_BK is set to HI-z which gives SW_BK 5.0V.
The peak current of the motor is 9.5A and the peak phase current of the driver is 8A. The motor have 3 phases and at least two of them active at once. This means that the approximate minimum peak phase current needed for efficient control is: Ioutx = 9.5A / sqrt(3) ~ 5.48A. Therefore if cycle-by-cy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
AVDD 3.3V/30mA
Motor hall sensor takes 3.3.. 18V input.
5.0V/200mA
~1.40V
SW_BK can be used to power external devices up to 5V max 200mA
Motor Driver and Connectors
Motor driver used to power and monitor the motor parameters. Reference schematic: driver_seperate by Anton Östman

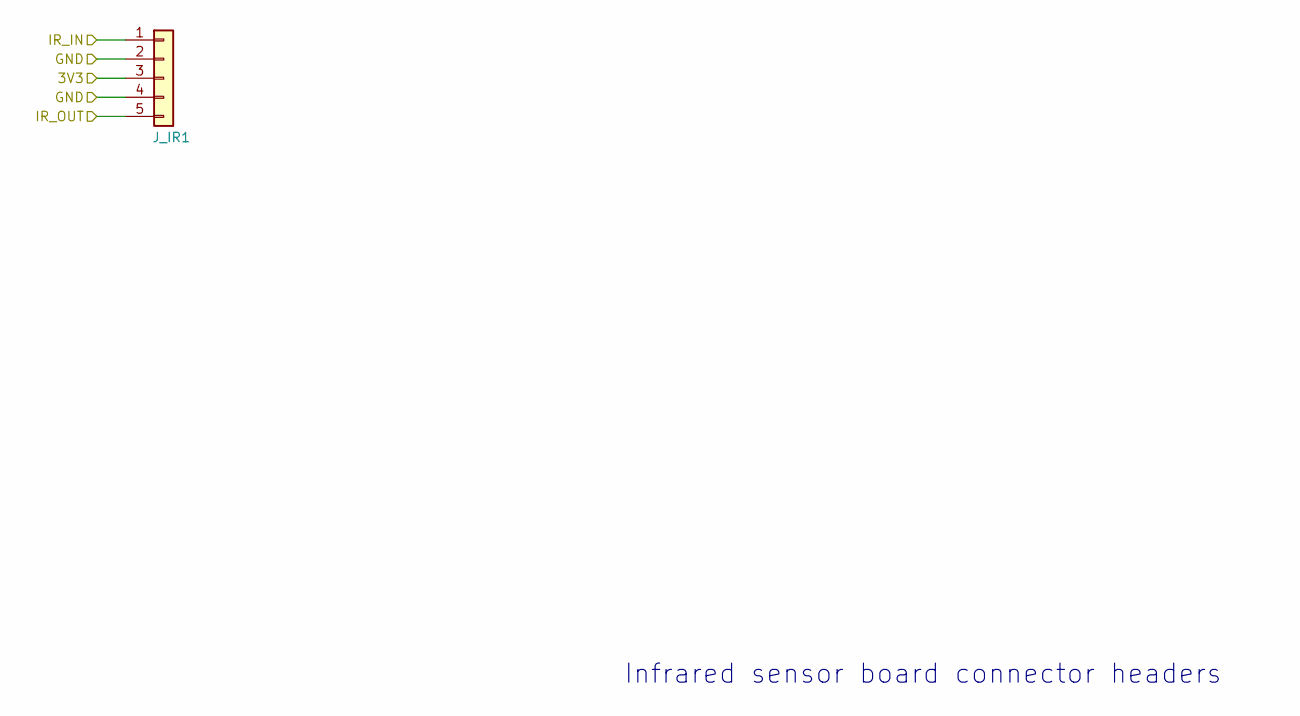
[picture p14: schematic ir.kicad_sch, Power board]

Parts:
J_IR1: Connector_Generic:Conn_01x05; PinHeader_1x05_P2.54mm_Vertical_SMD_Pin1Left

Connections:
3V3: J_IR1.3; also elsewhere on the board
/IR/IR_IN: J_IR1.1; also elsewhere on the board
/IR/IR_OUT: J_IR1.5; also elsewhere on the board
GND: J_IR1.2, J_IR1.4; also elsewhere on the board

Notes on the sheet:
Infrared sensor board connector headers

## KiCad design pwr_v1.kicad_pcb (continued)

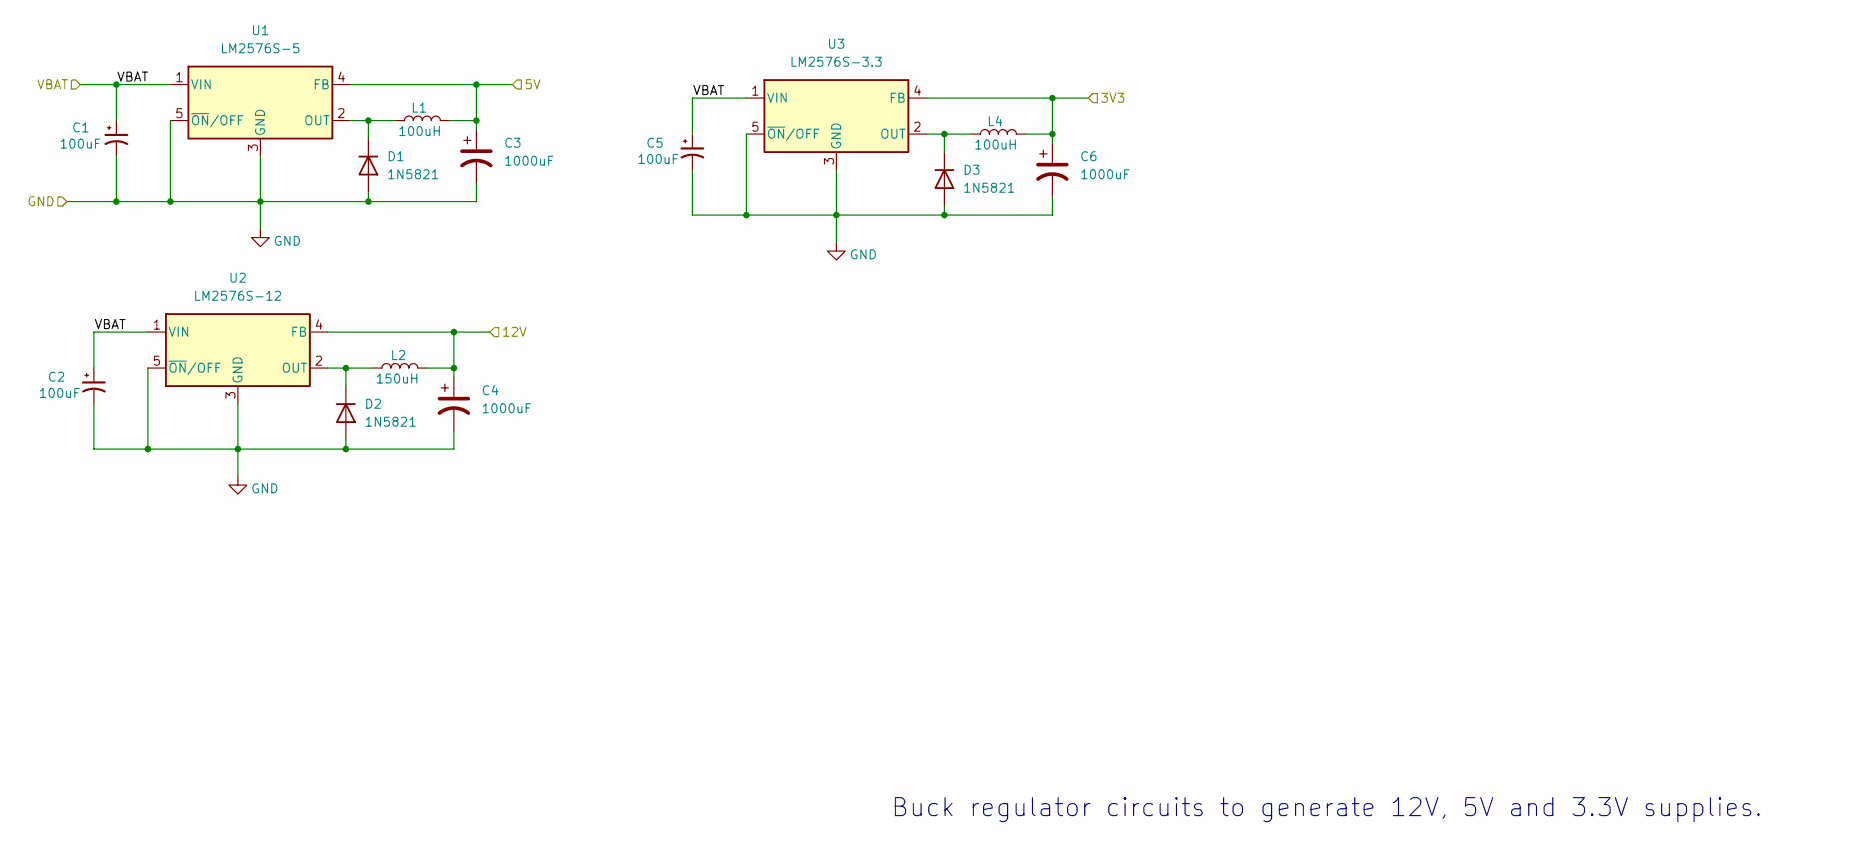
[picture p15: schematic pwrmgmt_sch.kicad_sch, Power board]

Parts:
C1, C2, C5: 100uF; CP_Elec_8x10
C3: 1000uF; CP_Elec_8x10.5
C4, C6: 1000uF; CP_Elec_10x10.5
D1, D2, D3: 1N5821; D_DO-201AD_P15.24mm_Horizontal
L1, L4: 100uH; L_Sunlord_MWSA1206S-101
L2: 150uH; L_TaiTech_TMPC1265_13.5x12.5mm
U1: LM2576S-5; TO-263-5_TabPin3
U2: LM2576S-12; TO-263-5_TabPin3
U3: LM2576S-3.3; TO-263-5_TabPin3

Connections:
3V3: C6.1, L4.2, U3.4 (FB); also elsewhere on the board
5V: C3.1, L1.2, U1.4 (FB); also elsewhere on the board
12V: C4.1, L2.2, U2.4 (FB); also elsewhere on the board
GND: C1.2, C2.2, C3.2, C4.2, C5.2, C6.2, D1.2 (A), D2.2 (A), D3.2 (A), U1.3 (GND), U1.5 (~ON/OFF), U2.3 (GND), U2.5 (~ON/OFF), U3.3 (GND), U3.5 (~ON/OFF); also elsewhere on the board
unnamed: D1.1 (K), L1.1, U1.2 (OUT)
unnamed: D2.1 (K), L2.1, U2.2 (OUT)
unnamed: D3.1 (K), L4.1, U3.2 (OUT)
VBAT: C1.1, C2.1, C5.1, U1.1 (VIN), U2.1 (VIN), U3.1 (VIN); also elsewhere on the board

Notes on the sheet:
Buck regulator circuits to generate 12V, 5V and 3.3V supplies.

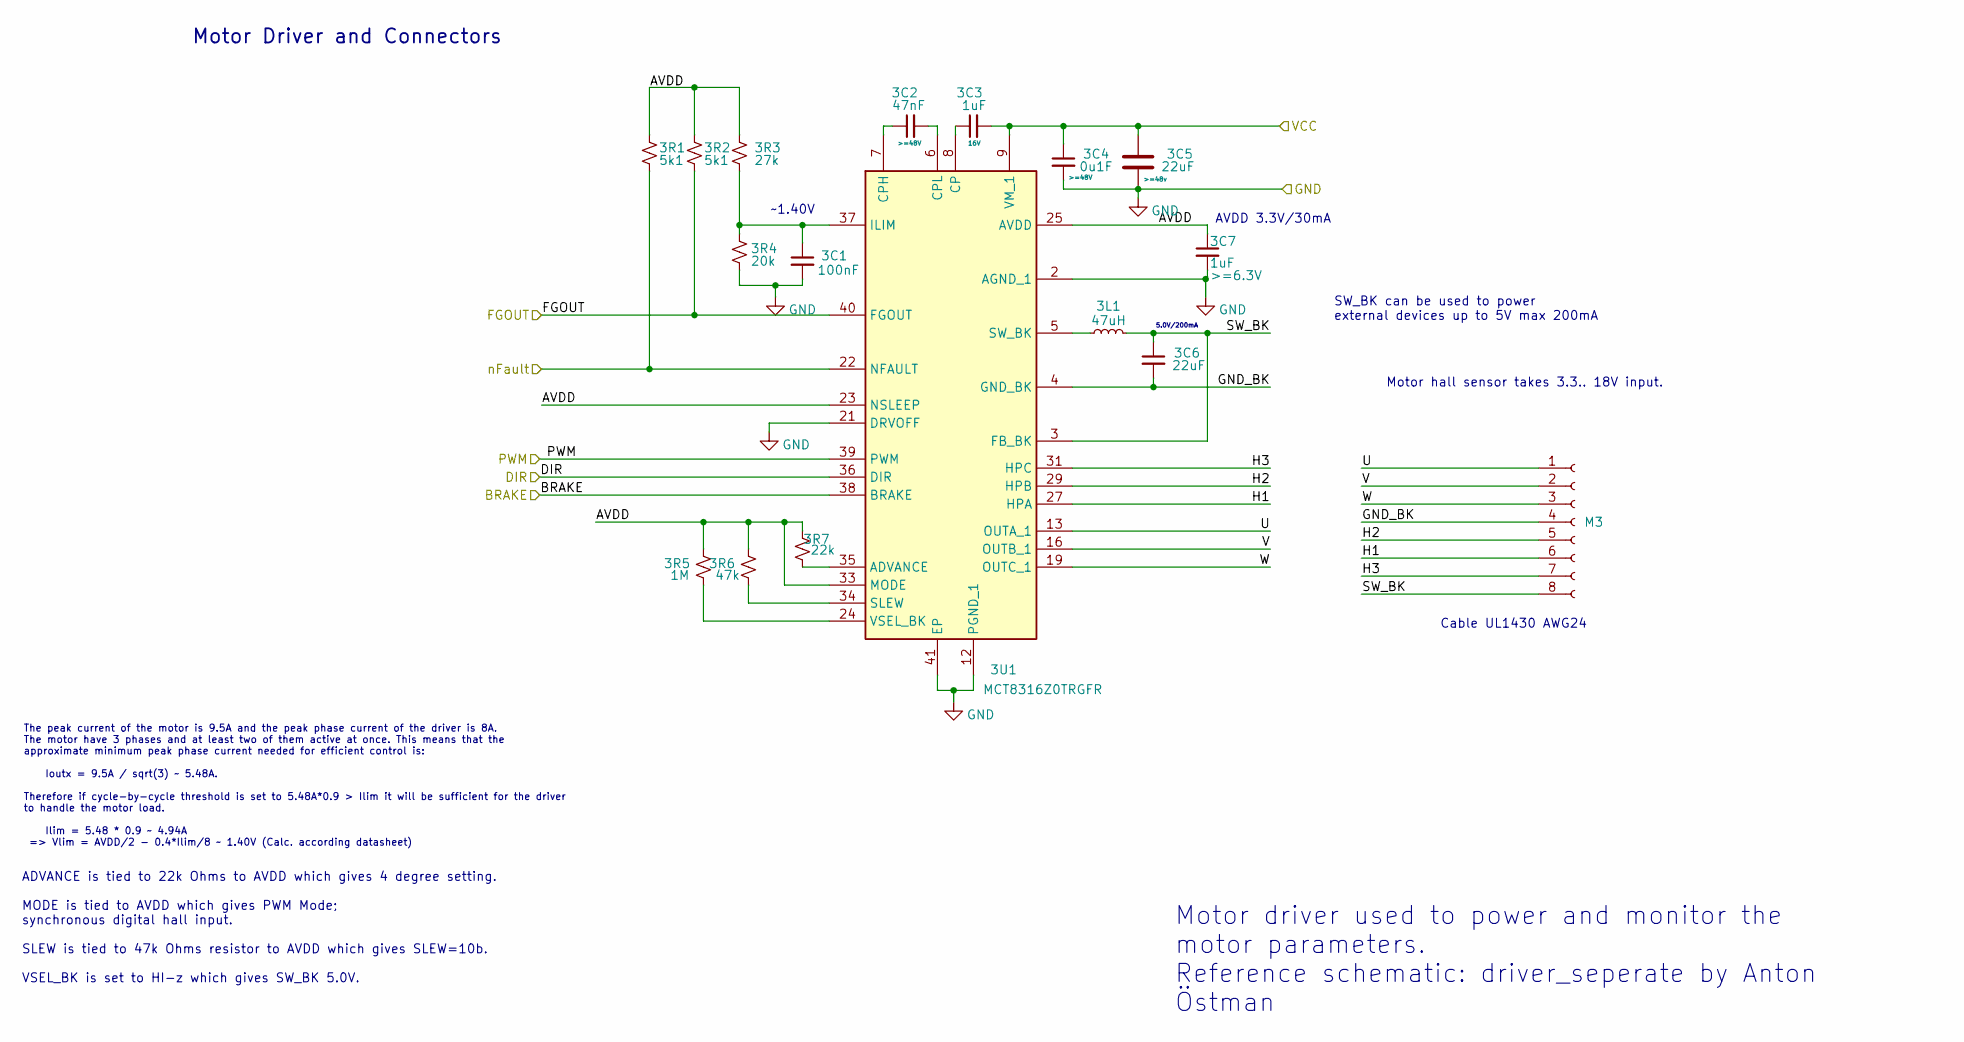
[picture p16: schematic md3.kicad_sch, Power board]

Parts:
3C1: 100nF; C_0402_1005Metric
3C2: 47nF; C_0402_1005Metric; Voltage >=48V
3C3: 1uF; C_0402_1005Metric; Voltage 16V
3C4: 0u1F; C_0402_1005Metric; Voltage >=48V
3C5: 22uF; C_2220_5750Metric; Voltage >=48v
3C6: 22uF; C_0402_1005Metric
3C7: 1uF; C_0402_1005Metric; Voltage >=6.3V
3L1: 47uH; L_0805_2012Metric
3R1, 3R2: 5k1; R_0603_1608Metric
3R3: 27k; R_0603_1608Metric
3R4: 20k; R_0603_1608Metric
3R5: 1M; R_0805_2012Metric
3R6: 47k; R_0402_1005Metric
3R7: 22k; R_0402_1005Metric
3U1: MCT8316Z0TRGFR; RGF0040E-IPC_B; Mouser Part Number 595-CT8316Z0TQRGFRQ1
M3: Conn_01x08_Socket; PinHeader_1x08_P2.54mm_Vertical

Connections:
5V: 3R1.2, 3U1.22 (NFAULT); also elsewhere on the board
/MotorDriver3/AVDD: 3C7.1, 3R1.1, 3R2.1, 3R3.1, 3R5.2, 3R6.2, 3R7.2, 3U1.23 (NSLEEP), 3U1.25 (AVDD), 3U1.33 (MODE)
/MotorDriver3/BRAKE: 3U1.38 (BRAKE); also elsewhere on the board
/MotorDriver3/DIR: 3U1.36 (DIR); also elsewhere on the board
/MotorDriver3/FGOUT: 3R2.2, 3U1.40 (FGOUT); also elsewhere on the board
/MotorDriver3/GND_BK: 3C6.2, 3U1.4 (GND_BK), M3.4
/MotorDriver3/H1: 3U1.27 (HPA), M3.6
/MotorDriver3/H2: 3U1.29 (HPB), M3.5
/MotorDriver3/H3: 3U1.31 (HPC), M3.7
/MotorDriver3/PWM: 3U1.39 (PWM); also elsewhere on the board
/MotorDriver3/SW_BK: 3C6.1, 3L1.2, 3U1.3 (FB_BK), M3.8
/MotorDriver3/U: 3U1.13 (OUTA_1), 3U1.14 (OUTA_2), M3.1
/MotorDriver3/V: 3U1.16 (OUTB_1), 3U1.17 (OUTB_2), M3.2
/MotorDriver3/W: 3U1.19 (OUTC_1), 3U1.20 (OUTC_2), M3.3
GND: 3C1.2, 3C4.2, 3C5.2, 3C7.2, 3R4.2, 3U1.2 (AGND_1), 3U1.12 (PGND_1), 3U1.15 (PGND_2), 3U1.18 (PGND_3), 3U1.21 (DRVOFF), 3U1.26 (AGND_2), 3U1.41 (EP); also elsewhere on the board
unnamed: 3R7.1, 3U1.35 (ADVANCE)
unnamed: 3C3.1, 3U1.8 (CP)
unnamed: 3C2.1, 3U1.7 (CPH)
unnamed: 3C2.2, 3U1.6 (CPL)
unnamed: 3C1.1, 3R3.2, 3R4.1, 3U1.37 (ILIM)
unnamed: 3R6.1, 3U1.34 (SLEW)
unnamed: 3L1.1, 3U1.5 (SW_BK)
unnamed: 3R5.1, 3U1.24 (VSEL_BK)
VBAT: 3C3.2, 3C4.1, 3C5.1, 3U1.9 (VM_1), 3U1.10 (VM_2), 3U1.11 (VM_3); also elsewhere on the board

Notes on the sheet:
5.0V/200mA
ADVANCE is tied to 22k Ohms to AVDD which gives 4 degree setting. MODE is tied to AVDD which gives PWM Mode; synchronous digital hall input. SLEW is tied to 47k Ohms resistor to AVDD which gives SLEW=10b. VSEL_BK is set to HI-z which gives SW_BK 5.0V.
Cable UL1430 AWG24
The peak current of the motor is 9.5A and the peak phase current of the driver is 8A. The motor have 3 phases and at least two of them active at once. This means that the approximate minimum peak phase current needed for efficient control is: Ioutx = 9.5A / sqrt(3) ~ 5.48A. Therefore if cycle-by-cy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
Motor hall sensor takes 3.3.. 18V input.
~1.40V
AVDD 3.3V/30mA
SW_BK can be used to power external devices up to 5V max 200mA
Motor Driver and Connectors
Motor driver used to power and monitor the motor parameters. Reference schematic: driver_seperate by Anton Östman

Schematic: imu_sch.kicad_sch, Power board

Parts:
C12, C13: 100nF; C_0402_1005Metric
R2, R3: 1k; R_0603_1608Metric
U4: LSM6DSLTR; LGA-14_3x2.5mm_P0.5mm_LayoutBorder3x4y

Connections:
3V3: C12.1, C13.1, R2.1, R3.1, U4.5 (VDDIO), U4.8 (VDD); also elsewhere on the board
/IMU/CS: U4.12 (CS); also elsewhere on the board
/IMU/INT1: U4.4 (INT1); also elsewhere on the board
/IMU/INT2: U4.9 (INT2); also elsewhere on the board
/IMU/SCL: R2.2, U4.13 (SCL); also elsewhere on the board
/IMU/SDA: R3.2, U4.14 (SDA); also elsewhere on the board
/IMU/SDO_SAO: U4.1 (SDO/SA0); also elsewhere on the board
GND: C12.2, C13.2, U4.2 (SDX), U4.3 (SCX), U4.6 (GND), U4.7 (GND); also elsewhere on the board

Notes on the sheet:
CS-0 : SPI mode CS-1 : I2C mode
IMU unit used to measure various motion parameters. Reference schematic: imu_LSM6DSL by Li Ang Hu

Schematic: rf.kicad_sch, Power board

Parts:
J_RF1: Conn_02x04_Counter_Clockwise; PinSocket_2x04_P2.54mm_Vertical

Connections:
3V3: J_RF1.8; also elsewhere on the board
/RF/CE: J_RF1.2; also elsewhere on the board
/RF/CSN: J_RF1.7; also elsewhere on the board
/RF/IRQ: J_RF1.5; also elsewhere on the board
/RF/MISO: J_RF1.4; also elsewhere on the board
/RF/MOSI: J_RF1.6; also elsewhere on the board
/RF/SCK: J_RF1.3; also elsewhere on the board
GND: J_RF1.1; also elsewhere on the board

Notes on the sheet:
RF Module socket

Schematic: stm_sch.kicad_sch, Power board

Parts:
CN11, CN12: Conn_02x36_Odd_Even; PinHeader_2x36_P2.54mm_Vertical_SMD

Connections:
5V: CN11.6; also elsewhere on the board
/Battery Supervisor/M: CN12.65; also elsewhere on the board
/Battery Supervisor/O1: CN11.11; also elsewhere on the board
/Battery Supervisor/O2: CN11.56; also elsewhere on the board
/Battery Supervisor/O3: CN11.54; also elsewhere on the board
/Battery Supervisor/O4: CN11.9; also elsewhere on the board
/Battery Supervisor/O5: CN12.42; also elsewhere on the board
/Battery Supervisor/O6: CN11.38; also elsewhere on the board
/STM32/CE_NRF: CN12.4; also elsewhere on the board
/STM32/CS_NRF: CN12.3; also elsewhere on the board
/STM32/IR_CS: CN11.30; also elsewhere on the board
/STM32/IR_IN: CN12.12; also elsewhere on the board
/STM32/IR_INT1: CN12.35; also elsewhere on the board
/STM32/IR_INT2: CN12.37; also elsewhere on the board
/STM32/IR_OUT: CN12.14; also elsewhere on the board
/STM32/KICKER_CHARGE: CN12.18; also elsewhere on the board
/STM32/KICKER_CS: CN12.49; also elsewhere on the board
/STM32/KICKER_DISCHARGE1: CN12.25; also elsewhere on the board
/STM32/KICKER_DISCHARGE2: CN12.16; also elsewhere on the board
/STM32/KICKER_ERR: CN12.30; also elsewhere on the board
/STM32/MISO: CN12.13; also elsewhere on the board
/STM32/MOSI: CN12.29; also elsewhere on the board
/STM32/MOTOR1_BREAK: CN12.22; also elsewhere on the board
/STM32/MOTOR1_ENCODER: CN11.4; also elsewhere on the board
/STM32/MOTOR1_PWM: CN12.52; also elsewhere on the board
/STM32/MOTOR1_REVERSE: CN12.17; also elsewhere on the board
/STM32/MOTOR2_BREAK: CN12.41; also elsewhere on the board
/STM32/MOTOR2_ENCODER: CN12.64; also elsewhere on the board
/STM32/MOTOR2_PWM: CN12.56; also elsewhere on the board
/STM32/MOTOR2_REVERSE: CN12.40; also elsewhere on the board
/STM32/MOTOR3_BREAK: CN12.43; also elsewhere on the board
/STM32/MOTOR3_ENCODER: CN11.32; also elsewhere on the board
/STM32/MOTOR3_PWM: CN12.55; also elsewhere on the board
/STM32/MOTOR3_REVERSE: CN12.44; also elsewhere on the board
/STM32/MOTOR4_BREAK: CN11.46; also elsewhere on the board
/STM32/MOTOR4_ENCODER: CN11.28; also elsewhere on the board
/STM32/MOTOR4_PWM: CN12.51; also elsewhere on the board
/STM32/MOTOR4_REVERSE: CN12.53; also elsewhere on the board
/STM32/MOTOR5_BREAK: CN11.62; also elsewhere on the board
/STM32/MOTOR5_ENCODER: CN11.17; also elsewhere on the board
/STM32/MOTOR5_PWM: CN11.50; also elsewhere on the board
/STM32/MOTOR5_REVERSE: CN11.48; also elsewhere on the board
/STM32/NRF_IRQ: CN12.26; also elsewhere on the board
/STM32/SCK: CN12.11; also elsewhere on the board
GND: CN11.8, CN11.19, CN11.20, CN11.22, CN11.49, CN11.60, CN12.9, CN12.20, CN12.39, CN12.54, CN12.63; also elsewhere on the board

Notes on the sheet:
STM32 Nucleo H755ZI devboard connector
Nucleo pin mapping details

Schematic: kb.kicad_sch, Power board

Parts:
J1: Conn_01x12_Pin; CON12_1X12_UR_DF13
Q1: BSS84; SOT-23
RK1, RK2, RK3, RK4, RK5, RK6, RK7, RK8: 100; R_0402_1005Metric
RK9, RK10: 10k; R_0402_1005Metric

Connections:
3V3: J1.10, RK9.1, RK10.1; also elsewhere on the board
12V: J1.11; also elsewhere on the board
/KB/CHG: RK5.2; also elsewhere on the board
/KB/CLK: RK2.2; also elsewhere on the board
/KB/CS: Q1.1 (G), RK1.2; also elsewhere on the board
/KB/DIS1: RK6.2, RK9.2; also elsewhere on the board
/KB/DIS2: RK7.2, RK10.2; also elsewhere on the board
/KB/ERR: RK8.2; also elsewhere on the board
/KB/MISO: Q1.3 (D); also elsewhere on the board
/KB/MOSI: RK4.2; also elsewhere on the board
GND: J1.9; also elsewhere on the board
unnamed: J1.1, RK1.1
unnamed: J1.2, RK2.1
unnamed: J1.3, RK3.1
unnamed: J1.4, RK4.1
unnamed: J1.5, RK5.1
unnamed: J1.6, RK6.1
unnamed: J1.7, RK7.1
unnamed: J1.8, RK8.1
unnamed: Q1.2 (S), RK3.2
VBAT: J1.12; also elsewhere on the board

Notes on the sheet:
Kicker board connector

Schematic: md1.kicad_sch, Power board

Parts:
1C1: 100nF; C_0402_1005Metric
1C2: 47nF; C_0402_1005Metric; Voltage >=48V
1C3: 1uF; C_0402_1005Metric; Voltage 16V
1C4: 0u1F; C_0402_1005Metric; Voltage >=48V
1C5: 22uF; C_2220_5750Metric; Voltage >=48v
1C6: 22uF; C_0402_1005Metric
1C7: 1uF; C_0402_1005Metric; Voltage >=6.3V
1L1: 47uH; L_0805_2012Metric
1R1, 1R2: 5k1; R_0603_1608Metric
1R3: 27k; R_0603_1608Metric
1R4: 20k; R_0603_1608Metric
1R5: 1M; R_0805_2012Metric
1R6: 47k; R_0402_1005Metric
1R7: 22k; R_0402_1005Metric
1U1: MCT8316Z0TRGFR; RGF0040E-IPC_B; Mouser Part Number 595-CT8316Z0TQRGFRQ1
M1: Conn_01x08_Socket; PinHeader_1x08_P2.54mm_Vertical

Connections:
5V: 1R1.2, 1U1.22 (NFAULT); also elsewhere on the board
/MotorDriver1/AVDD: 1C7.1, 1R1.1, 1R2.1, 1R3.1, 1R5.2, 1R6.2, 1R7.2, 1U1.23 (NSLEEP), 1U1.25 (AVDD), 1U1.33 (MODE)
/MotorDriver1/BRAKE: 1U1.38 (BRAKE); also elsewhere on the board
/MotorDriver1/DIR: 1U1.36 (DIR); also elsewhere on the board
/MotorDriver1/FGOUT: 1R2.2, 1U1.40 (FGOUT); also elsewhere on the board
/MotorDriver1/GND_BK: 1C6.2, 1U1.4 (GND_BK), M1.4
/MotorDriver1/H1: 1U1.27 (HPA), M1.6
/MotorDriver1/H2: 1U1.29 (HPB), M1.5
/MotorDriver1/H3: 1U1.31 (HPC), M1.7
/MotorDriver1/PWM: 1U1.39 (PWM); also elsewhere on the board
/MotorDriver1/SW_BK: 1C6.1, 1L1.2, 1U1.3 (FB_BK), M1.8
/MotorDriver1/U: 1U1.13 (OUTA_1), 1U1.14 (OUTA_2), M1.1
/MotorDriver1/V: 1U1.16 (OUTB_1), 1U1.17 (OUTB_2), M1.2
/MotorDriver1/W: 1U1.19 (OUTC_1), 1U1.20 (OUTC_2), M1.3
GND: 1C1.2, 1C4.2, 1C5.2, 1C7.2, 1R4.2, 1U1.2 (AGND_1), 1U1.12 (PGND_1), 1U1.15 (PGND_2), 1U1.18 (PGND_3), 1U1.21 (DRVOFF), 1U1.26 (AGND_2), 1U1.41 (EP); also elsewhere on the board
unnamed: 1R7.1, 1U1.35 (ADVANCE)
unnamed: 1C3.1, 1U1.8 (CP)
unnamed: 1C2.1, 1U1.7 (CPH)
unnamed: 1C2.2, 1U1.6 (CPL)
unnamed: 1C1.1, 1R3.2, 1R4.1, 1U1.37 (ILIM)
unnamed: 1R6.1, 1U1.34 (SLEW)
unnamed: 1L1.1, 1U1.5 (SW_BK)
unnamed: 1R5.1, 1U1.24 (VSEL_BK)
VBAT: 1C3.2, 1C4.1, 1C5.1, 1U1.9 (VM_1), 1U1.10 (VM_2), 1U1.11 (VM_3); also elsewhere on the board

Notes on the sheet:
Motor hall sensor takes 3.3.. 18V input.
ADVANCE is tied to 22k Ohms to AVDD which gives 4 degree setting. MODE is tied to AVDD which gives PWM Mode; synchronous digital hall input. SLEW is tied to 47k Ohms resistor to AVDD which gives SLEW=10b. VSEL_BK is set to HI-z which gives SW_BK 5.0V.
The peak current of the motor is 9.5A and the peak phase current of the driver is 8A. The motor have 3 phases and at least two of them active at once. This means that the approximate minimum peak phase current needed for efficient control is: Ioutx = 9.5A / sqrt(3) ~ 5.48A. Therefore if cycle-by-cy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
~1.40V
Cable UL1430 AWG24
SW_BK can be used to power external devices up to 5V max 200mA
5.0V/200mA
Motor Driver and Connectors
AVDD 3.3V/30mA
Motor driver used to power and monitor the motor parameters. Reference schematic: driver_seperate by Anton Östman

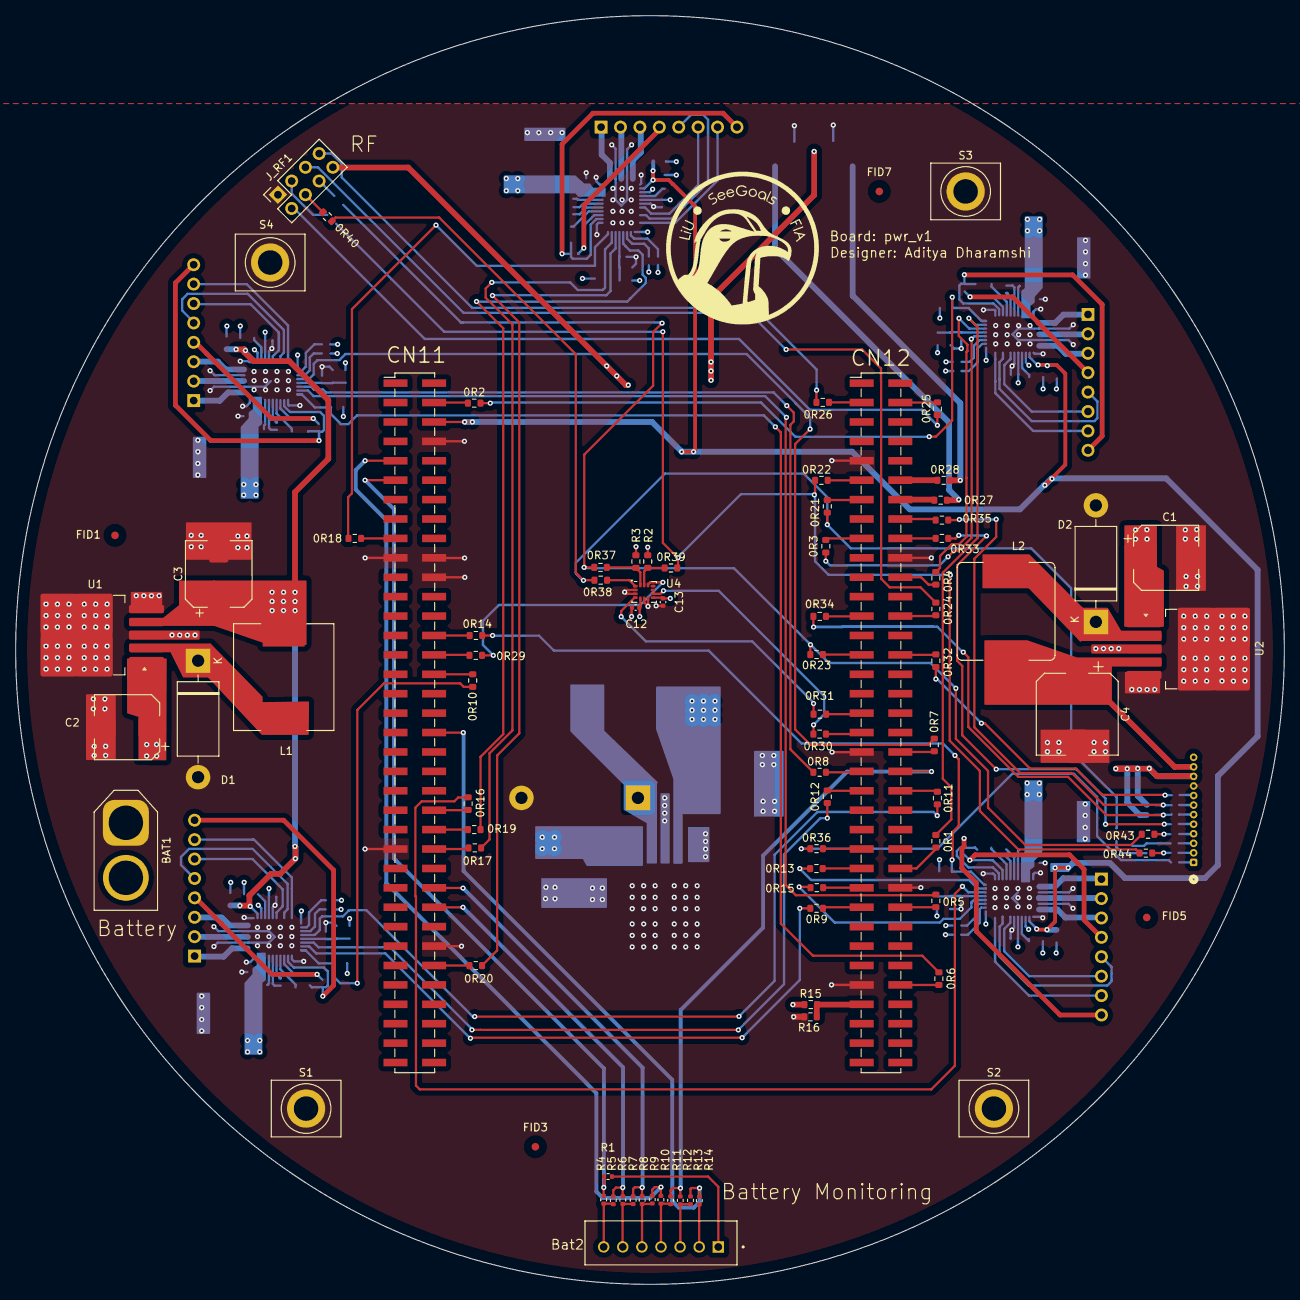
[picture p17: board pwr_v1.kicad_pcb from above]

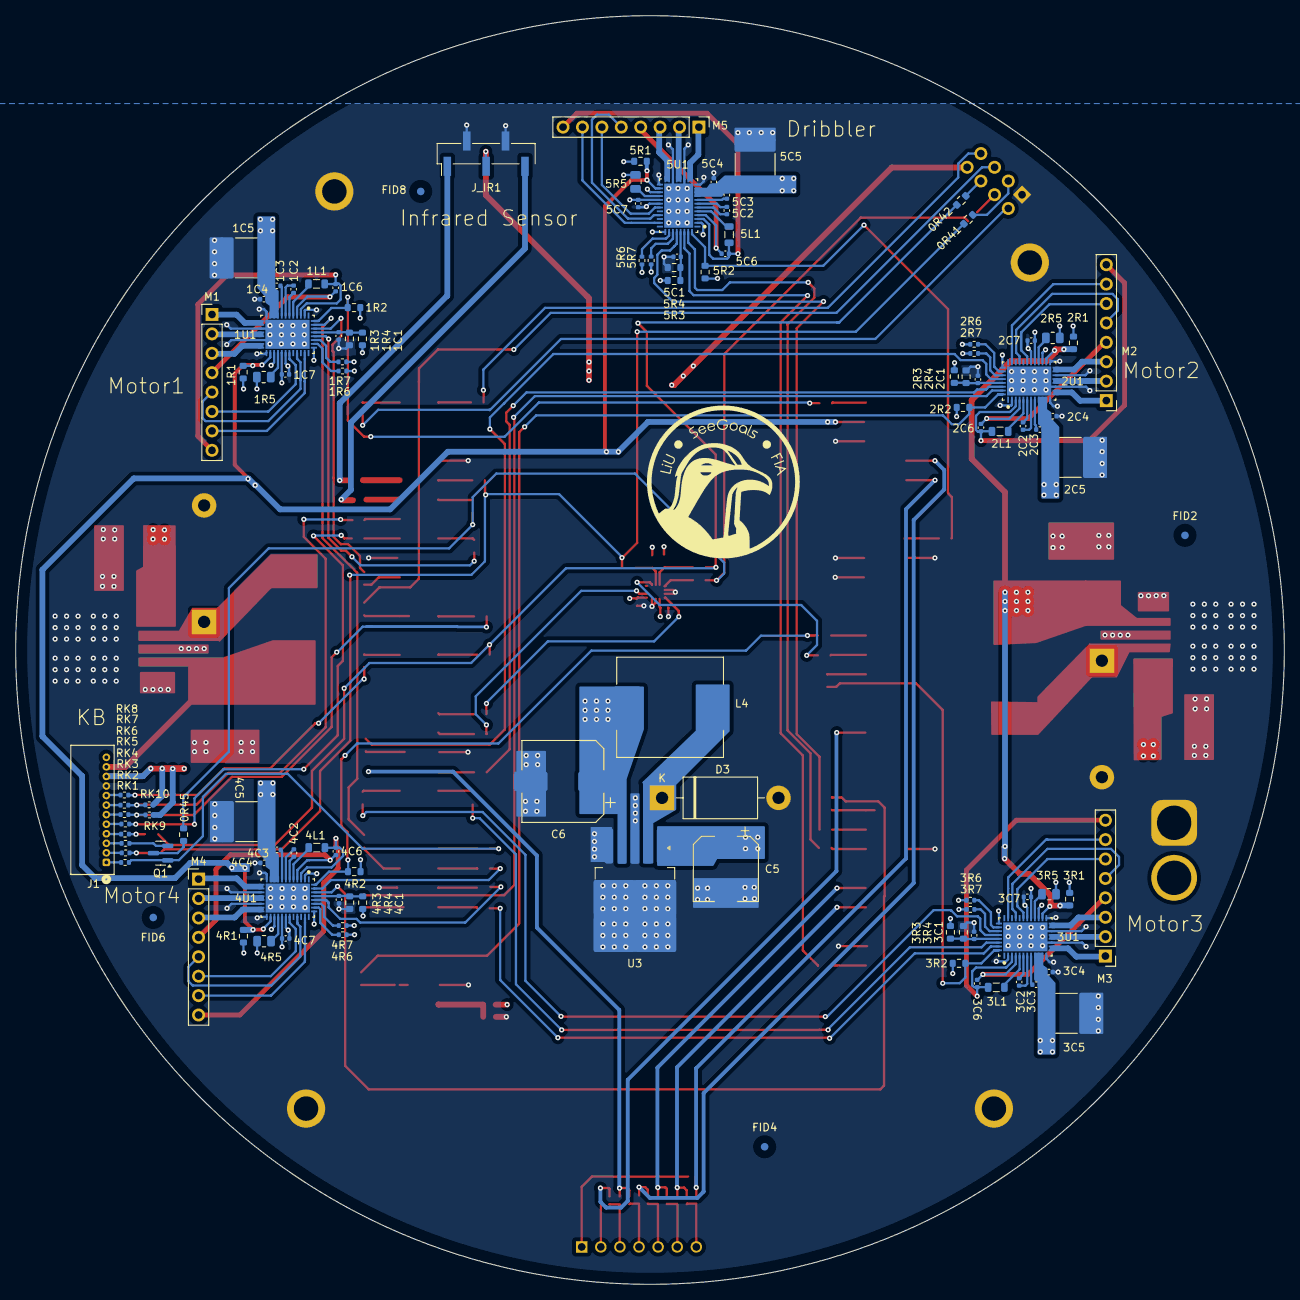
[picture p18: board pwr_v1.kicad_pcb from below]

Board: 4 copper layers, 166.0 x 166.0 mm, 194 parts (110 on the bottom side), 197 nets.
